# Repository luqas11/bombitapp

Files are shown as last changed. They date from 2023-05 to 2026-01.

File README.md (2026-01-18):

# bombitapp

### What is this
This project is a **device that controls and protects electric water pump systems**, built with an **ESP8266** based board, and operated from a mobile app developed in [React Native](https://reactnative.dev/). The device is able to preventively cut off power from the pump engines when an abnormal functioning is detected.

It's designed to operate over this preexisting pump setup:
- 2 220VAC 1/2 HP pumps.
- 2 water tanks.
- 2 water level sensors, placed inside the tanks and made by an on/off switch that turns on when the tank gets emptied and turns off when the filling process is complete. That switch operates directly at 220VAC and it's signal is plugged in to the pumps.
- 2 separated pipe circuits, each one connected to a different tank and pump. 

For different mechanical reasons, the sensors sometimes fail and keep the pumps engines running indefinitely, until manually fixed. If this happens, both the engines and the tanks could result **physically damaged** if the problem isn't solved quickly. This device's idea is to **cut pump power** if the sensor is sending the signal over a time period that exceeds some predefined threshold, to protect the setup. From a mobile app, the user can **resume the power after fixing the problem**, or **read the tank filling time history** to get an idea of the expected values. 

### Components
The project has the following components and features:

##### Hardware
- An ESP8266 based board, able to connect to the home Wi-Fi network.
- A custom PCB, to allow the ESP mounting and connection to the inputs and ouputs.
- 2 220VAC inputs, to recieve the tank water level signal. The ESP will read that signal to make it's decissions.
- 2 220VAC outputs, to power the water pumps. The ESP will power them with the water level sensor signal or not, depending on it's decissions.
- 1 5VCC input, to power the ESP board.
- 1 LED to indicate the WiFi connection status.

##### Firmware
- A sketch written in C++ and loaded to the ESP.
- Serves a webpage that allows the user to initially configure the WiFi credentials.
- Allows the level sensor signal to reach the output and power the pump until a time threshold is exceeded. After that, the connection is stopped to prevent the engine to keep working. If the signal stops before the threshold (i. e. the filling was successful), nothing happens.
- The time threshold can be setted via an HTTP request.
- Allows to resume the pump power via an HTTP request, overriding the stop state.
- The current engine working time can be get with an HTTP request.
- Allows to see the latest 10 engine run times via an HTTP request.
- Allows to see an average of all the previous engine run times via an HTTP request.
- The water level sensor status can be seen via an HTTP request (i. e. if it's on or off).

##### Mobile App
- A React Native mobile app compiled for Android.
- Gives a nice and human-friendly presentation layer for the firmware interaction, showing engine status and actions that can be made through HTTP.

### Screenshots
##### Mobile App
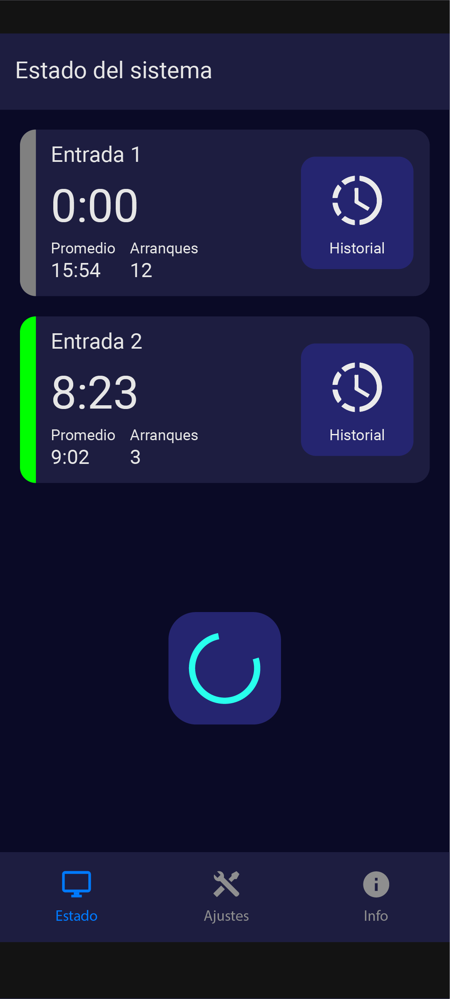
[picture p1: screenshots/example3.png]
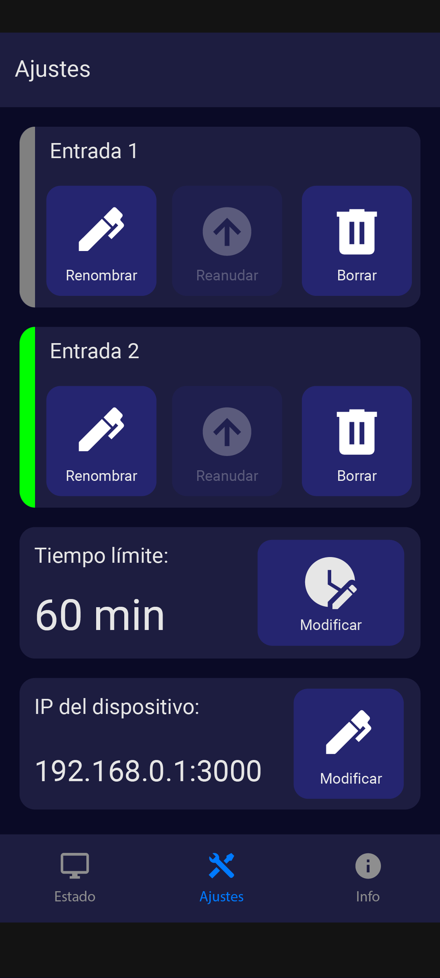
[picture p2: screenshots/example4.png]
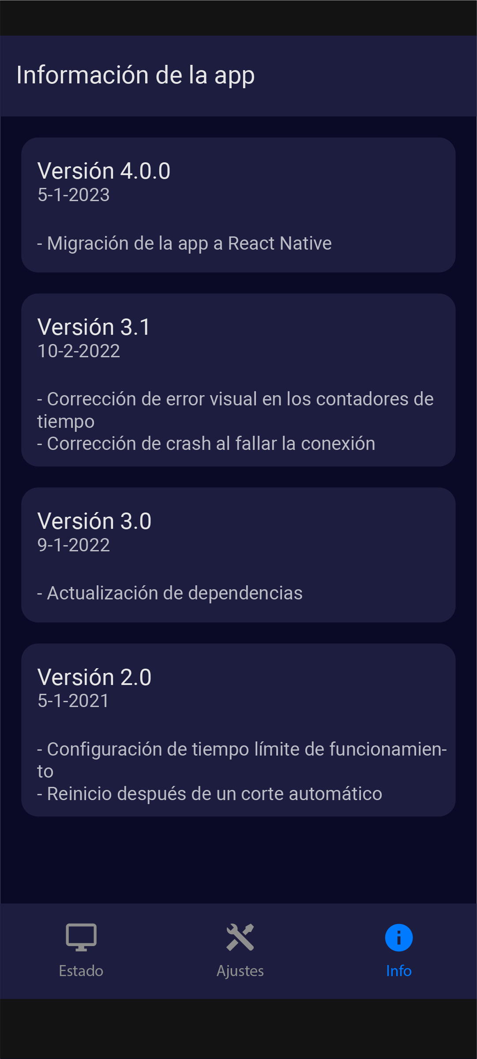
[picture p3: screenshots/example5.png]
    

##### PCB 3D model
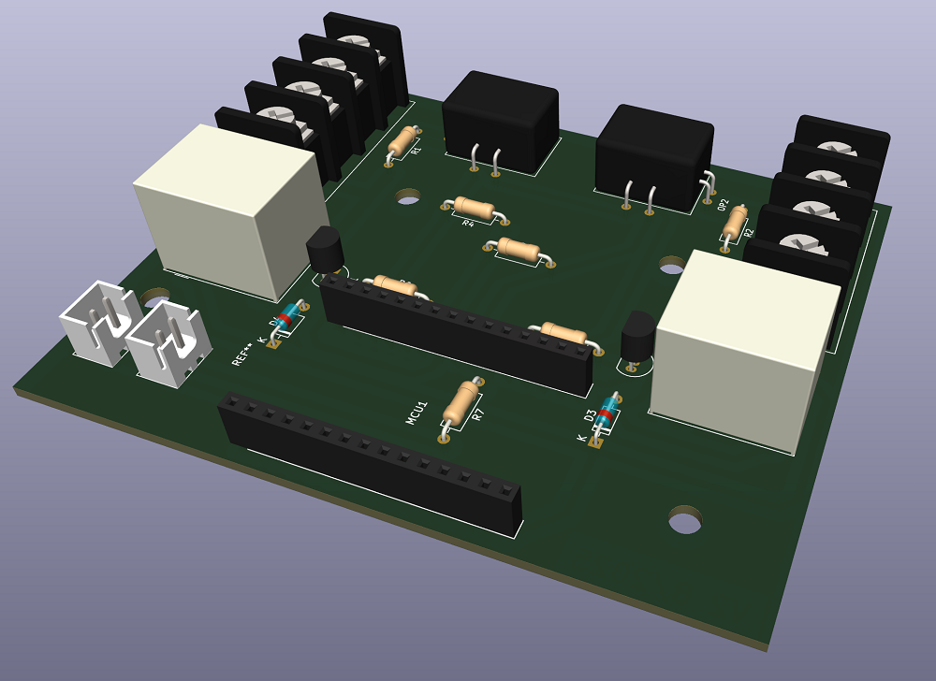
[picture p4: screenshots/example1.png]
 

##### Circuit schematic
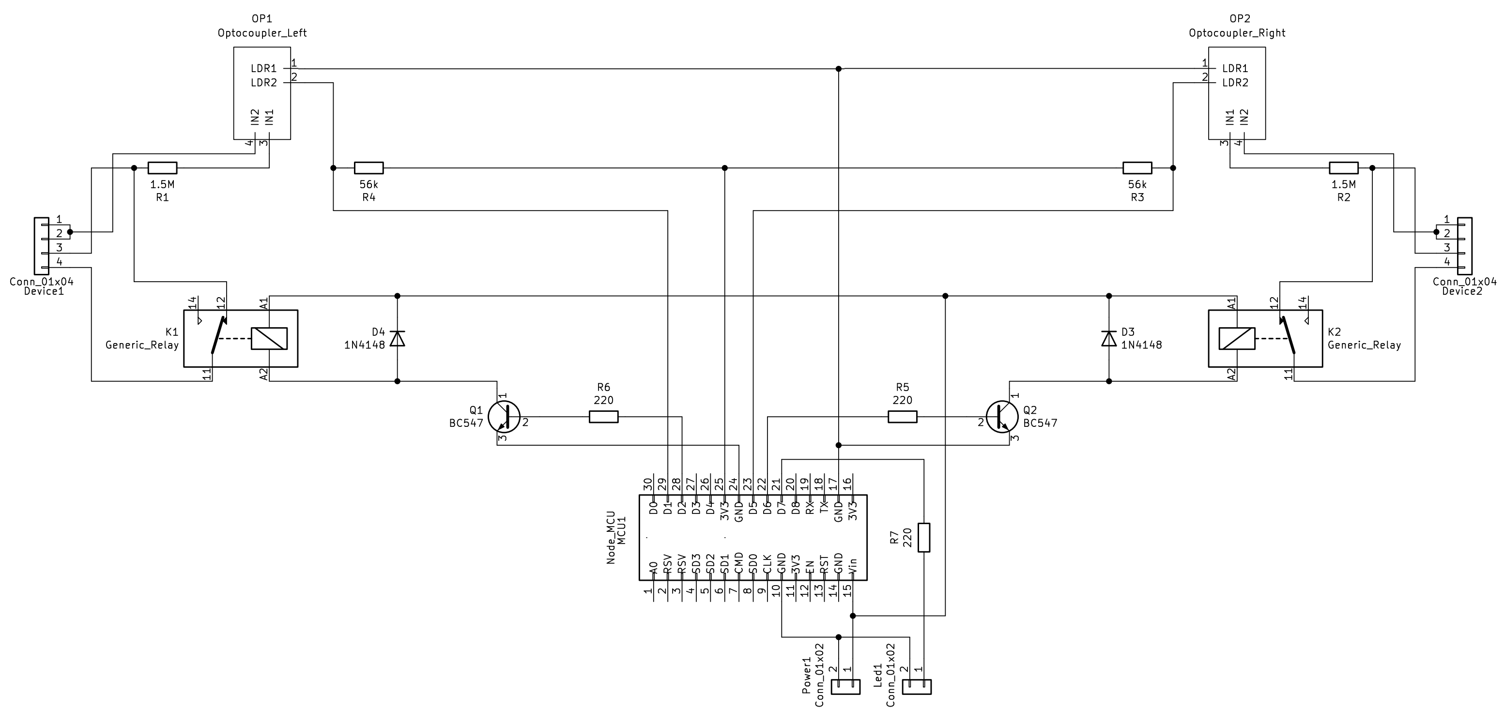
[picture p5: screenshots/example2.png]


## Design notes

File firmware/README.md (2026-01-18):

# Firmware

### How this works
This ESP8266 sketch connects the board to the WiFi network, and exposes some endpoints to get system status and set system configuration. The [Postman](https://www.postman.com/) collection in the root directory of this repository has complete examples and use cases of this API.

### API

`[GET] /status`  

Returns the current system status, including input status, device status, run counts and more. For example:
```
{
    "time_limit": 60,
    "devices": [
        {
            "status": 0,
            "current_time": 0,
            "mean_time": 25,
            "run_count": 10,
            "input_status": false,
            "history": [
                34,
                9,
                9,
                25,
                30,
                16,
                19,
                29,
                54,
                57
            ]
        },
        {
            "status": 0,
            "current_time": 0,
            "mean_time": 50,
            "run_count": 3,
            "input_status": false,
            "history": [
                28,
                42,
                81,
                0,
                0,
                0,
                0,
                0,
                0,
                0
            ]
        }
    ]
}
```

`[GET] /clear-history?device={id}`  

Clears the run time history of a specific device. For example, the query params could be:
```
/clear-history?device=0
```

`[GET] /change-time-limit?time_limit={time}`  

Sets the run time limit in minutes to trigger the forced stop mode, for all the devices in the system. For example, the query params could be:
```
/change-time-limit?time_limit=60
```

`[GET] /resume?device={id}`  

Resumes a device that is in forced stop mode. For example, the query params could be:
```
/resume?device=0
```

`[GET] /get-wifi-config`  

Returns the current WiFi configuration. For example:
```
{
    "ssid": "myssid"
}
```

`[GET] /set-wifi-config?ssid={ssid}&password={password}`  

Sets the WiFi configuration with the specified SSID and password. For example, the query params could be:
```
/set-wifi-config?ssid=myssid&password=mypassword
```

`[GET] /get-wifi-status`  

Returns the current WiFi connection status and IP address. For example:
```
{
    "status": 3,
    "ip": "192.168.1.100"
}
```

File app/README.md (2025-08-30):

# App
This **React Native** app allows the end-user to see the system status, and set the system configurations.

With it, the user can:
- See the current devices statuses
- See the run time history
- See the average run time
- Set the time threshold to stop a device
- Clear run time history
- Set the system IP, to send the requests to

### Development notes:
There is a mock created with [JSON Server](https://github.com/typicode/json-server/tree/v0) that allows the developer to have working endpoints to test the app against, without having to run the firmware in a board. The mock IP can be configured in the `mock` script inside the `package.json` file.

To launch the app in a device or an emulator, use:  
`npm run android`

To compile an APK, use:  
`npm run assemble`

To start the mock server, use:  
`npm run mock`

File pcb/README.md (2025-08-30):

# PCB

This is a PCB design that implements the connections between the 220VAC relays and optocoupliers and the ESP board, along with all the necessary 3D printed parts to enable component mounting. The circuit schematic and the PCB layout are printed in the `pcb-schematic.pdf` and `pcb-layout.pdf` files respectively.

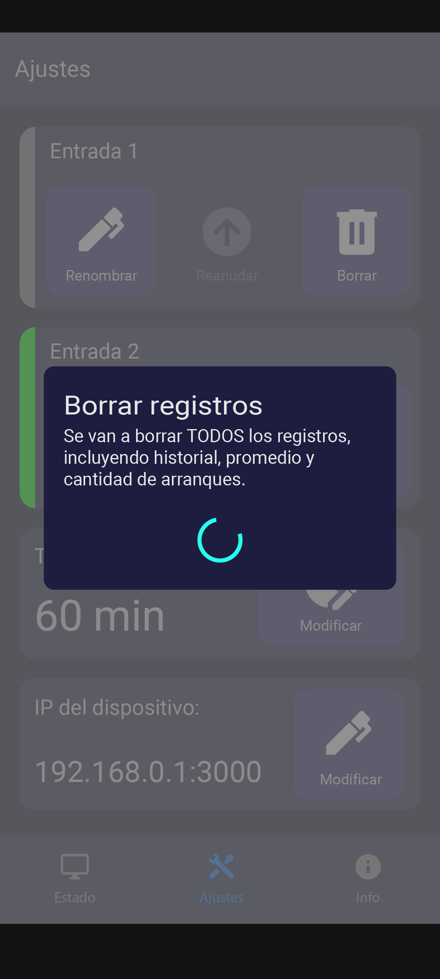
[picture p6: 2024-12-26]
app/ui_design/config_dialog_question_loading.png

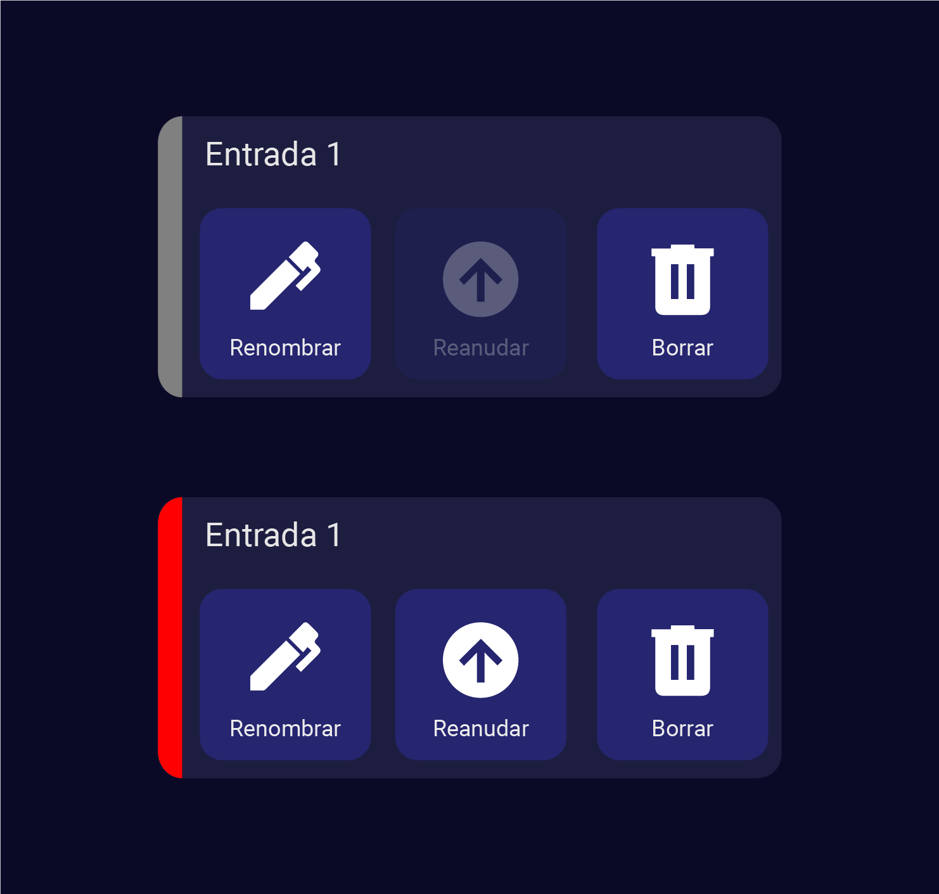
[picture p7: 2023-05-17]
app/ui_design/config_states.png

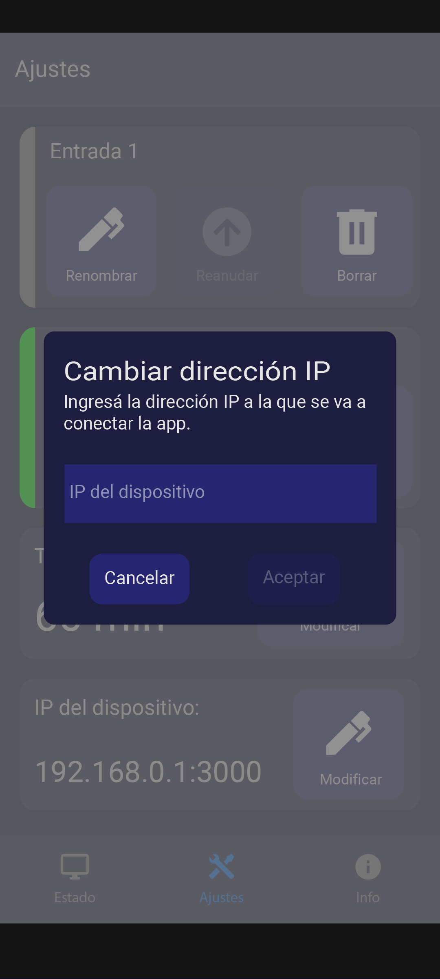
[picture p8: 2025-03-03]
app/ui_design/config_dialog_question_input_2.png

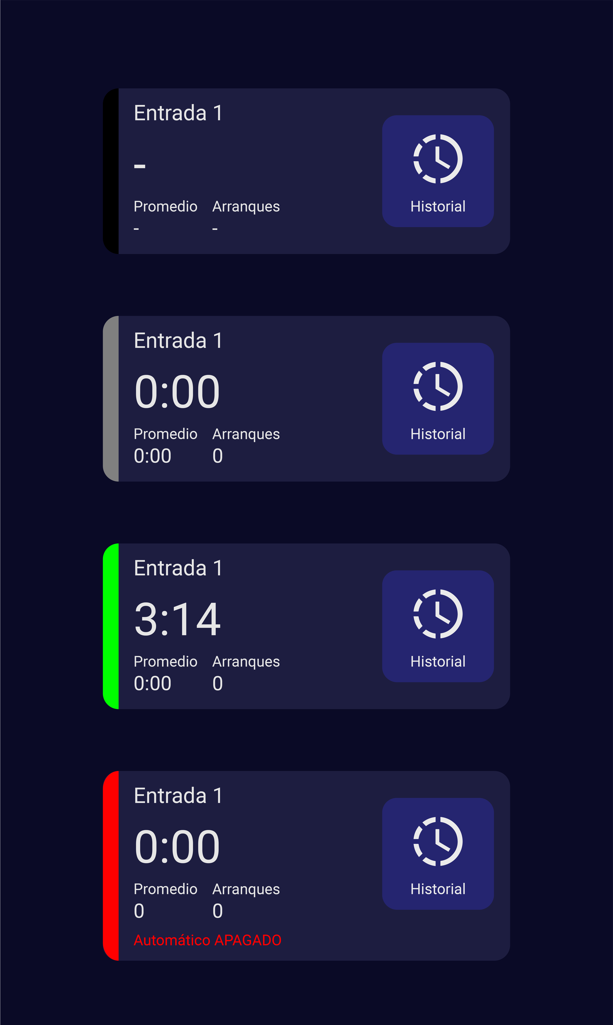
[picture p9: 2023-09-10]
app/ui_design/ouputs_statuses.png

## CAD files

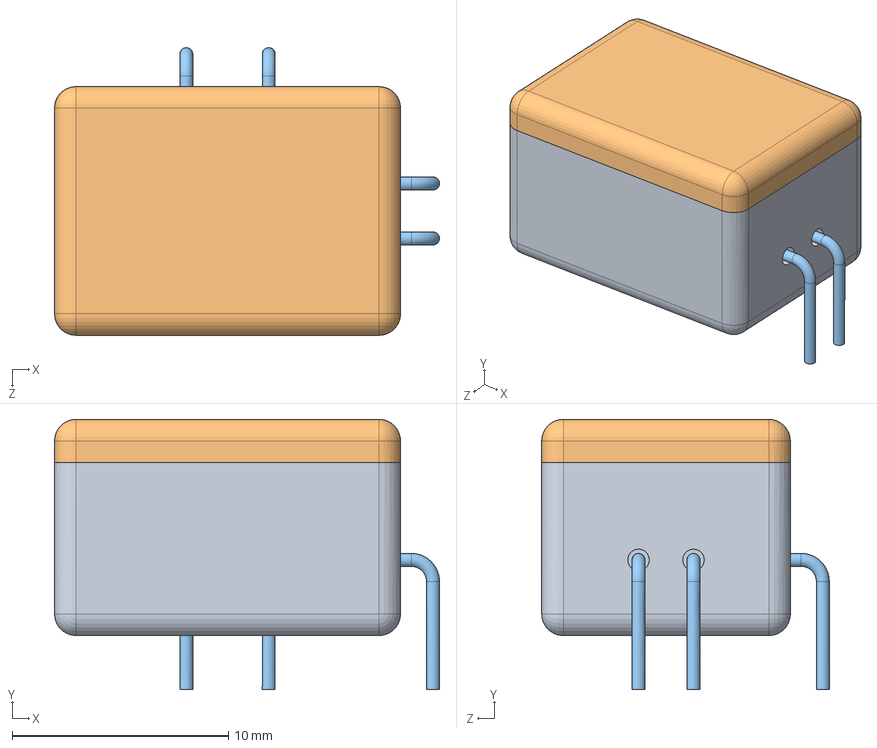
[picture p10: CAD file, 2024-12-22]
pcb/3D models/optocoupler.SLDASM
17.8 x 12.5 x 13.3 mm
optocoupler_box
optocoupler_lid
optocoupler_pin x 4

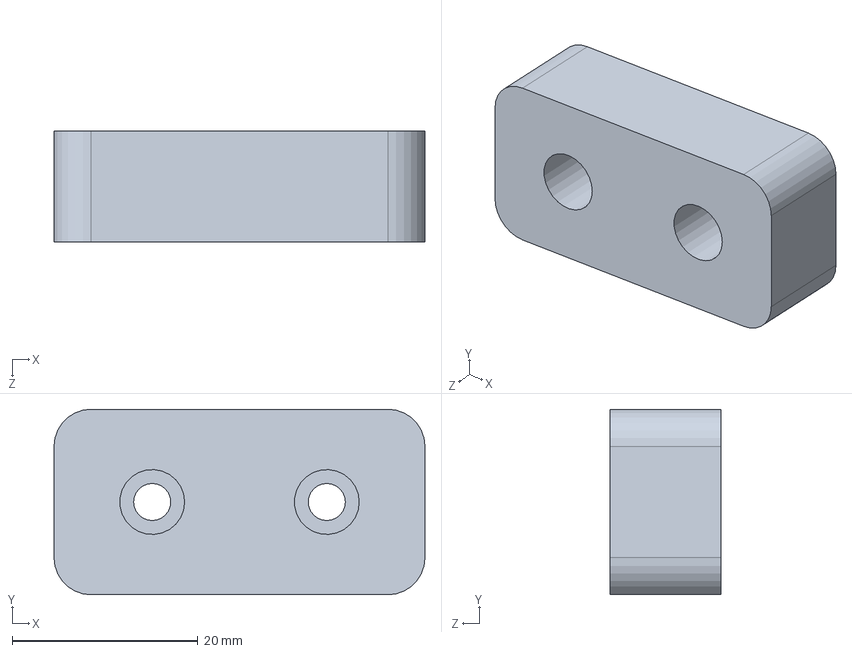
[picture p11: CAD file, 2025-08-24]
pcb/3D models/status_led_case.SLDPRT
40.0 x 20.0 x 12.0 mm

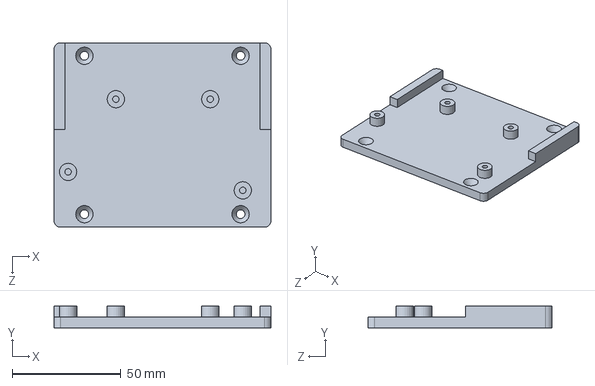
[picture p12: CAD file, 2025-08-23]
pcb/3D models/pcb_support.SLDPRT
100.0 x 10.0 x 85.0 mm

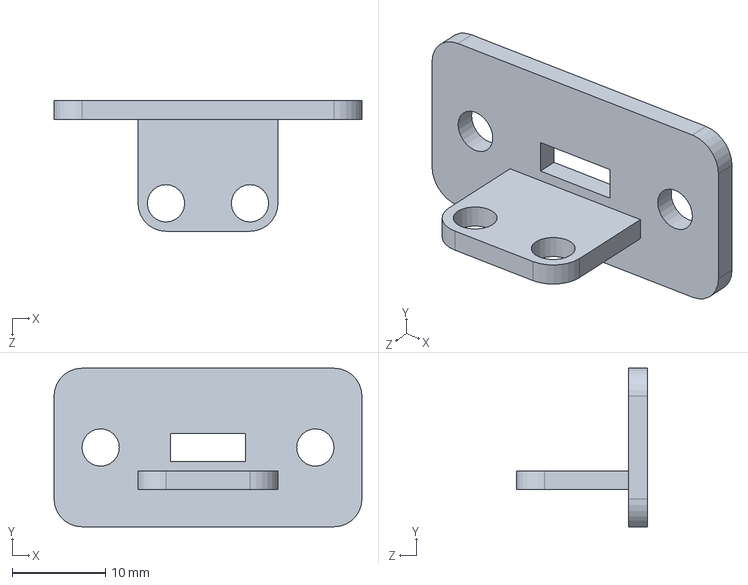
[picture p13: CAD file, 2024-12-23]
pcb/3D models/power_usb_socket.SLDPRT
33.0 x 17.0 x 14.0 mm

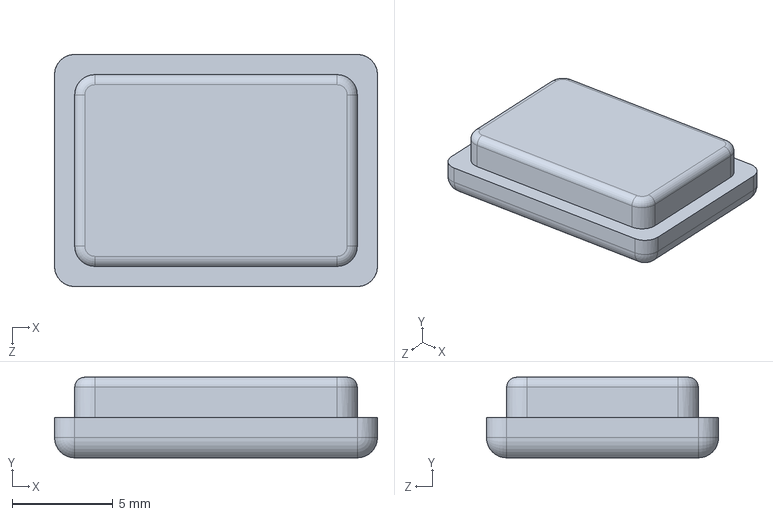
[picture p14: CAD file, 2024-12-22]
pcb/3D models/optocoupler_lid.SLDPRT
16.0 x 4.00 x 11.5 mm

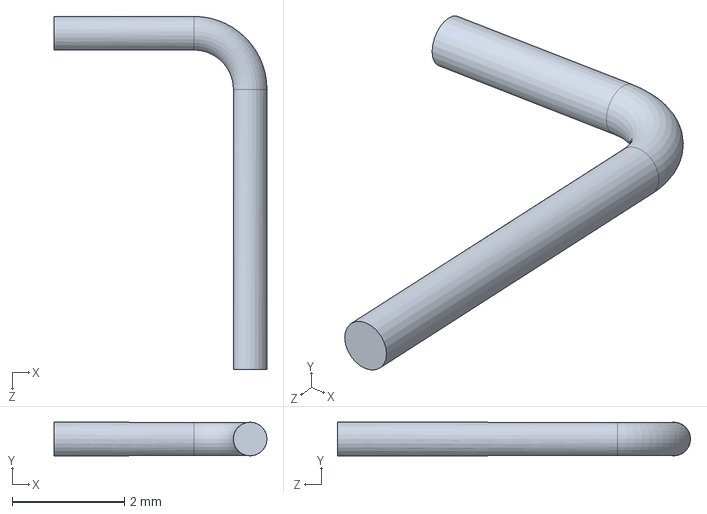
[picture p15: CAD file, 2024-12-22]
pcb/3D models/optocoupler_pin.SLDPRT
3.80 x 0.6 x 6.30 mm

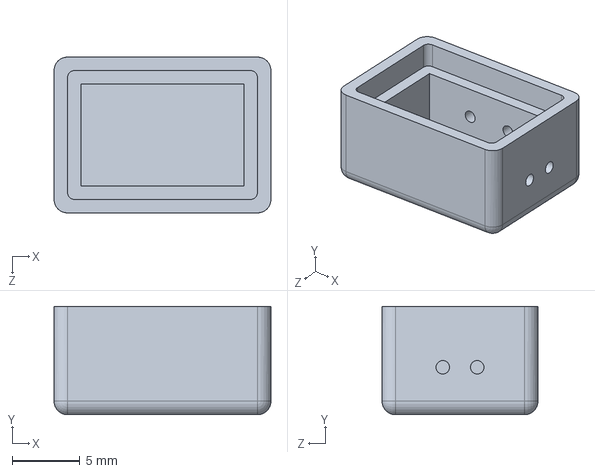
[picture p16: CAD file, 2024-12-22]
pcb/3D models/optocoupler_box.SLDPRT
16.0 x 8.00 x 11.5 mm

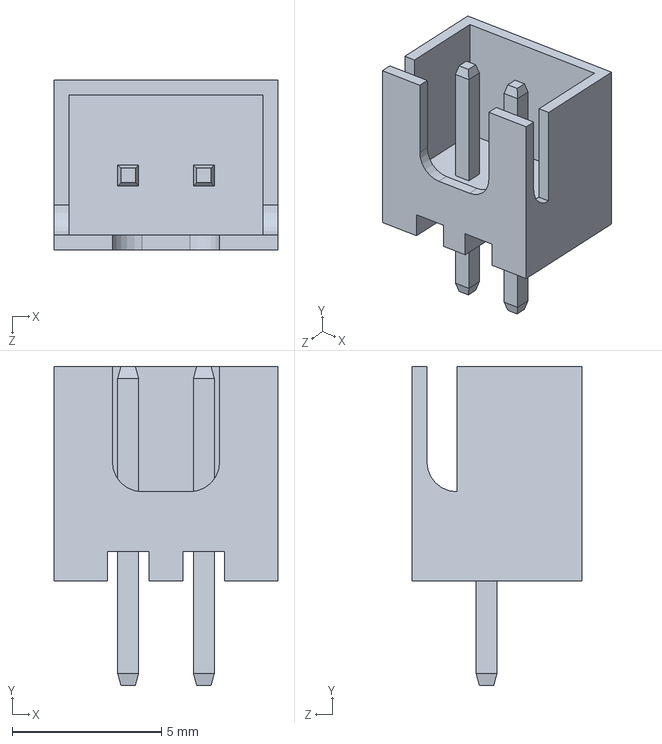
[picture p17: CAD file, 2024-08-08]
pcb/3D models/Pin_socket_2.SLDPRT
7.50 x 10.7 x 5.70 mm

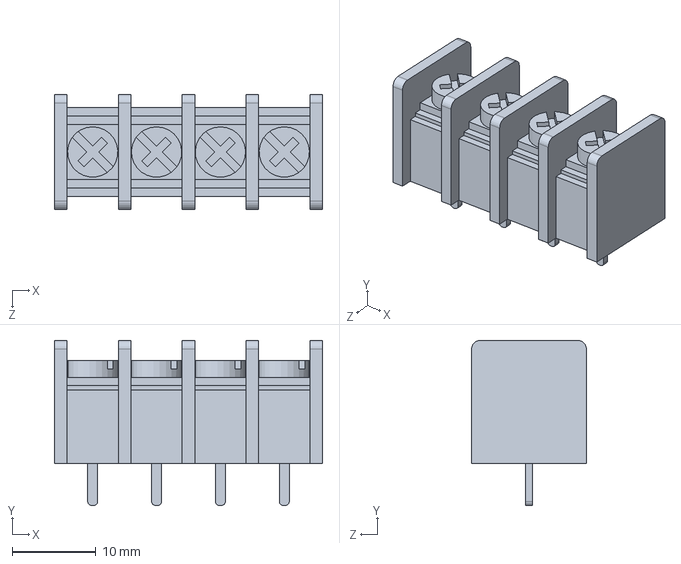
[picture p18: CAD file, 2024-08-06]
pcb/3D models/Terminal_block_4.SLDPRT
32.0 x 19.7 x 13.7 mm

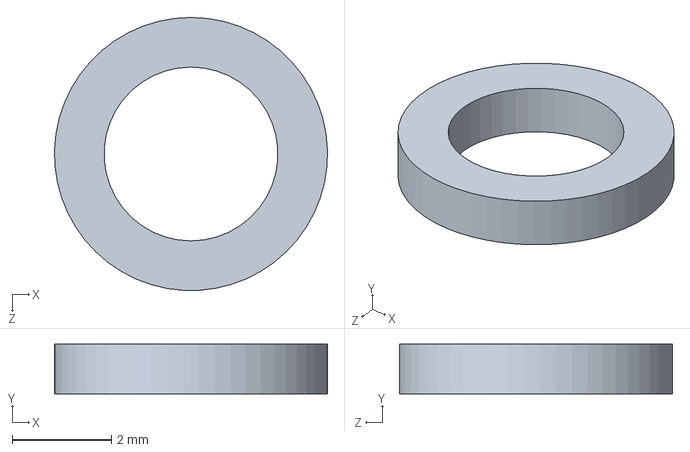
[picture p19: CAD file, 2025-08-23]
pcb/3D models/power_usb_washer.SLDPRT
5.50 x 1.00 x 5.50 mm

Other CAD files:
pcb/3D models/optocoupler_box.STL
pcb/3D models/optocoupler_lid.STL
pcb/3D models/pcb_support.STL
pcb/3D models/power_usb_socket.STL
pcb/3D models/power_usb_washer.STL
pcb/3D models/status_led_case.STL

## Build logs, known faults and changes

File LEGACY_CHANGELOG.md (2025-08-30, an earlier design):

# Control de bombas

## Versión 4.0.0 (5/1/2023)
*Prototipo probado con PCB, dos bombas y caja estanca.*
#### Android:
- Migración de la app a React Native

#### Software:
- Mejora de las respuestas de error
- Refactoreo de la lógica para recibir comandos

## Versión 3.1 (10/2/2022)

#### Android:
- Corrección de errores
- Actualización de dependencias

## Versión 3.0 (9/1/2022)
*Prototipo probado con PCB, dos bombas y caja estanca.*
#### Hardware:
- Rediseño del PCB para hacerlo más compacto y corregir errores
- Cambio de optoacopladores de 5V-5V por 220V-5V
- Construcción del nuevo PCB
- Armado de caja estanca con soporte para el PCB y tomas hembra para las bombas

## Versión 2.0 (4/1/2021)
*Prototipo probado con PCB propio y una única bomba.*
#### Software:
- Refactoreo de código general
- Parametrización de las direcciones de memoria de la EEPROM
- Refactoreo de variables para permitir escalabilidad a *n* entradas
- Respuestas de request formateadas como JSON
- Corte automático en caso de falla y reanudación manual
- Capacidad de recibir comandos para configurar el tiempo de corte automático, activar la reanudación manual y limpiar valores en EEPROM

#### Hardware:
- Diseño y construcción de PCB
- Dos entradas optoacopladas 5V-5V
- Dos salidas con relé 5V-220V

## Versión 1.x (N/A) 
*Prototipo probado en versión cableada, sin PCB y con dos bombas.*
#### Software:
- Guardado de tiempos en memoria EEPROM
- Comunicación vía HTTP request
- Respuesta en texto plano sin parsear, con estado actual de las bombas, historiales y promedios
- Entradas para dos bombas 

#### Hardware:
- Construcción de circuito cableado
- Dos entradas directas a 5V

## Versión 0.x (N/A)  
Sin documentar.

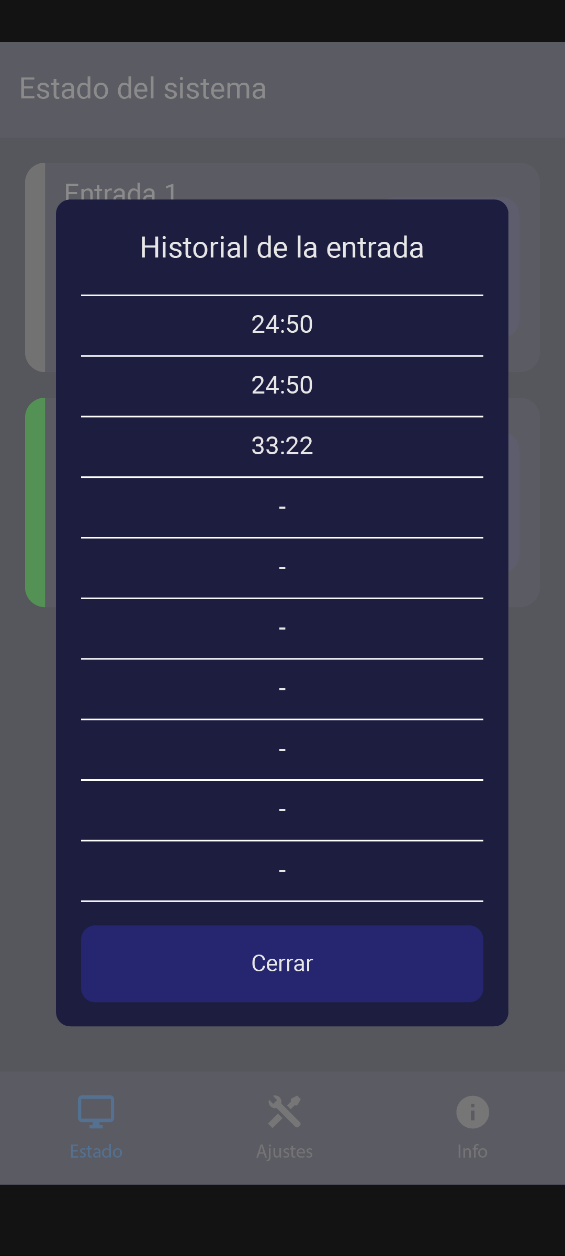
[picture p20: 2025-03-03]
app/ui_design/status_history.png

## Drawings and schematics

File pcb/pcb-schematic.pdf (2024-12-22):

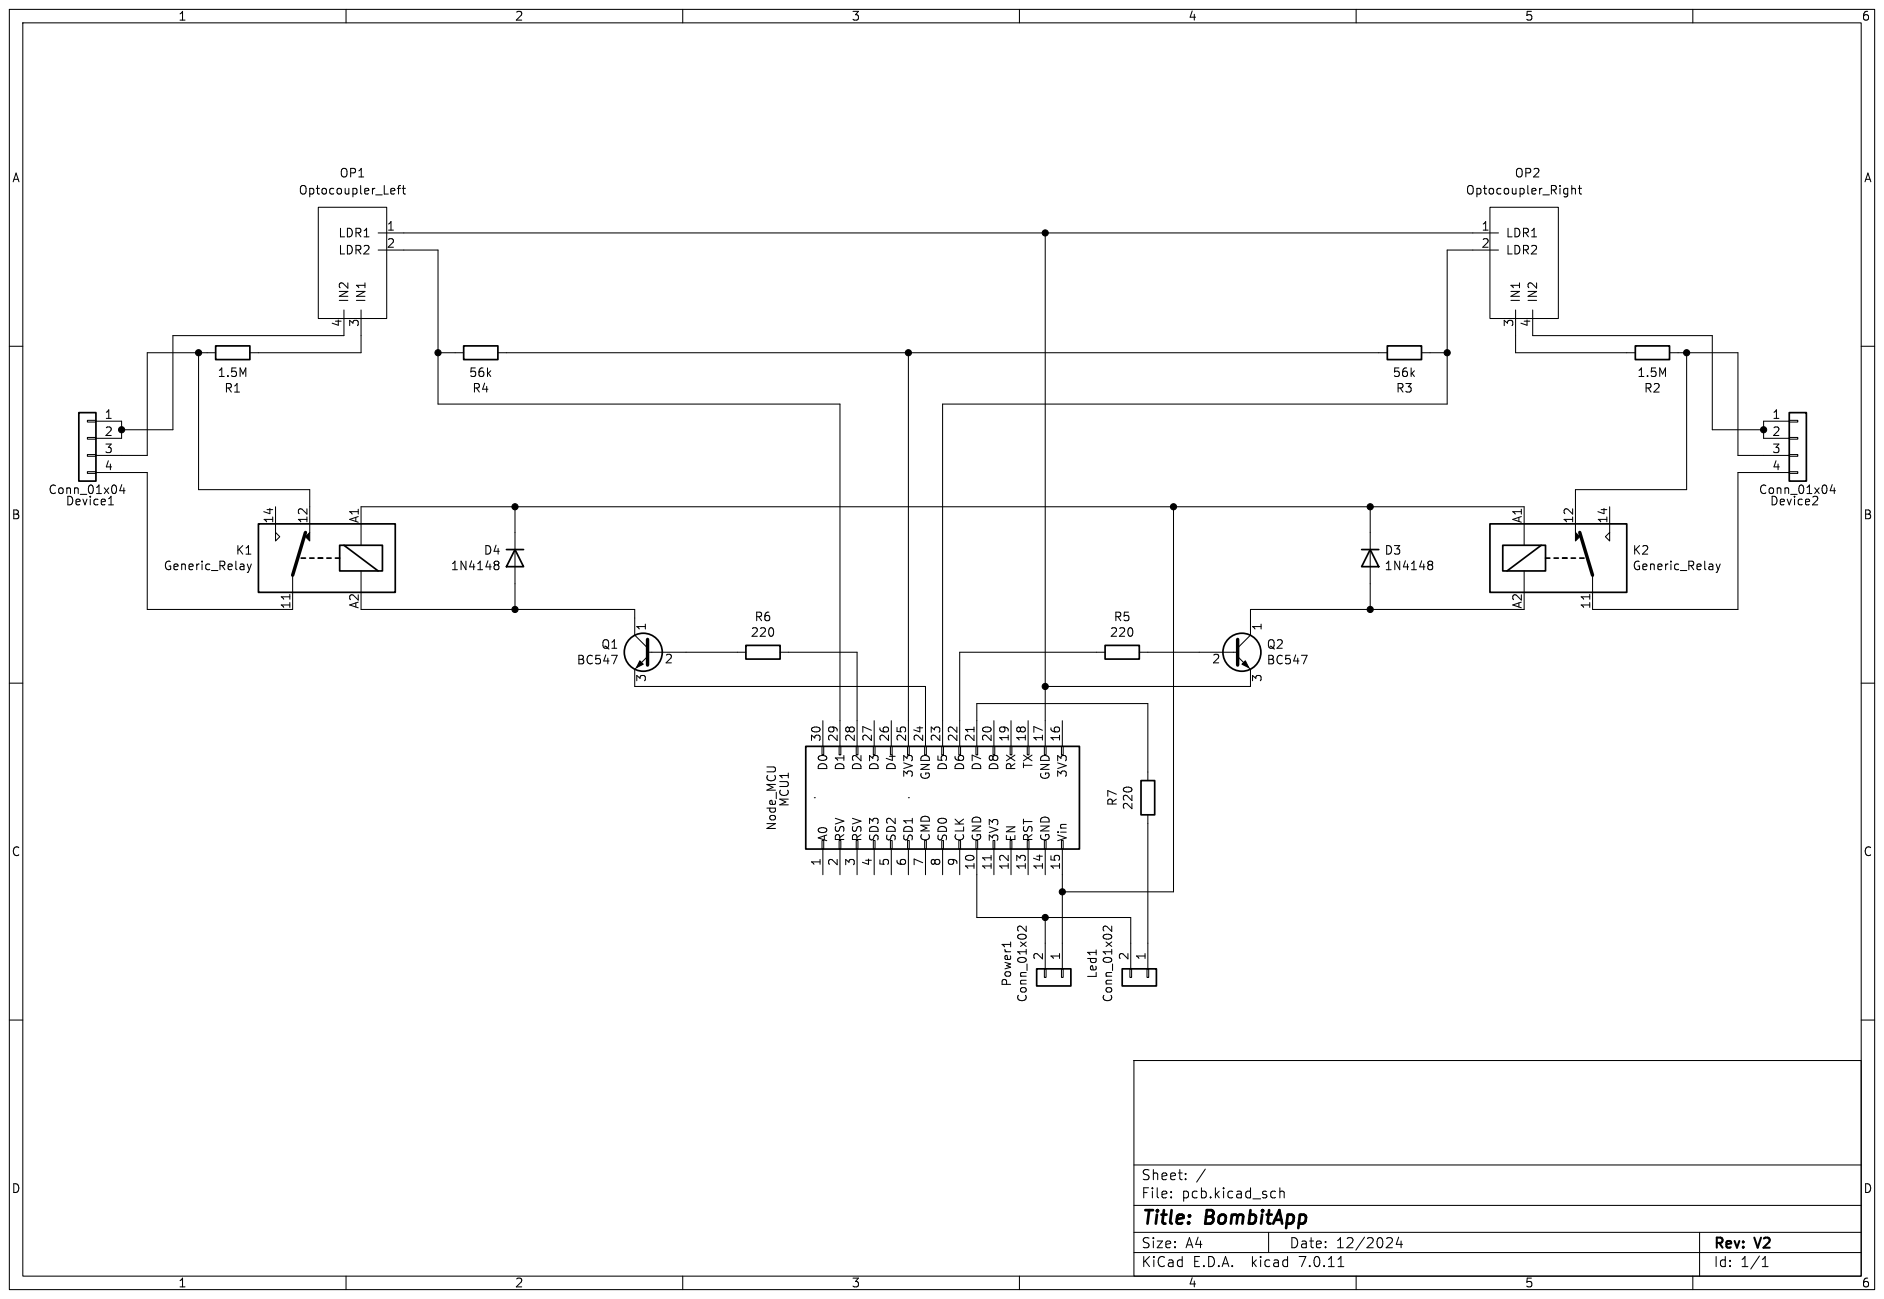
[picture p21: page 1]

1 GND 10 3V3 11 EN 12 RST 13 GND 14 Vin 15 3V3 16 GND 17 TX 18 RX 19 RSV

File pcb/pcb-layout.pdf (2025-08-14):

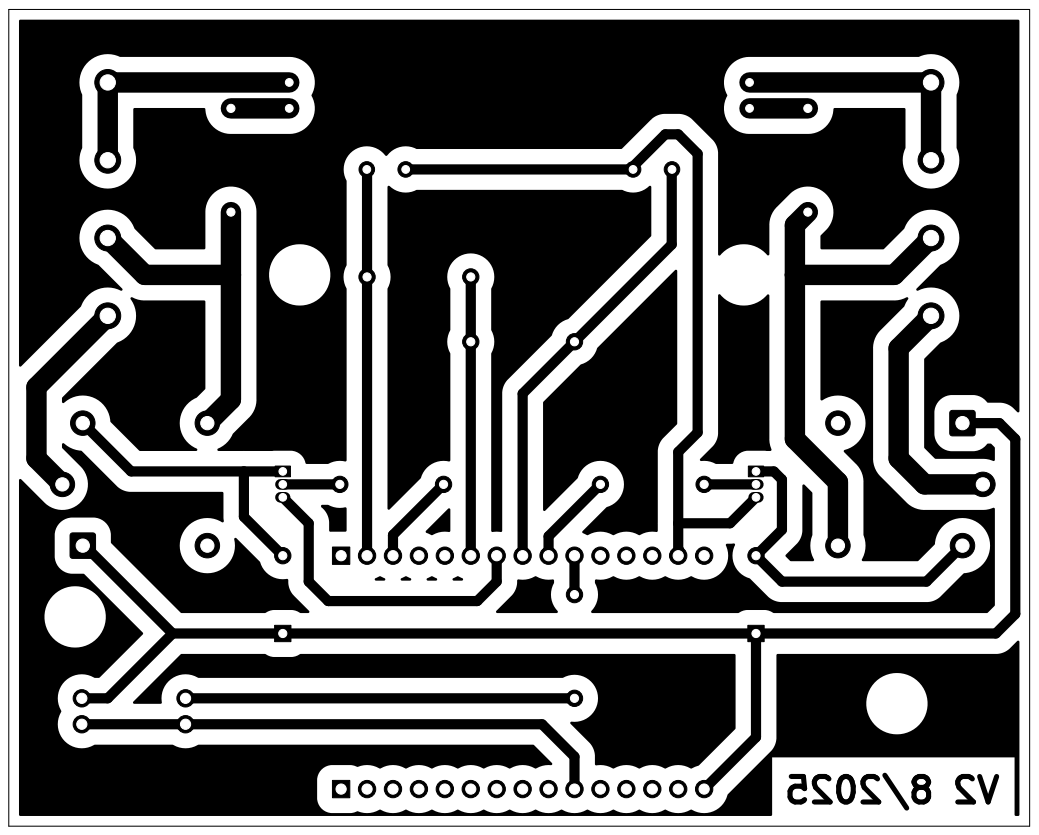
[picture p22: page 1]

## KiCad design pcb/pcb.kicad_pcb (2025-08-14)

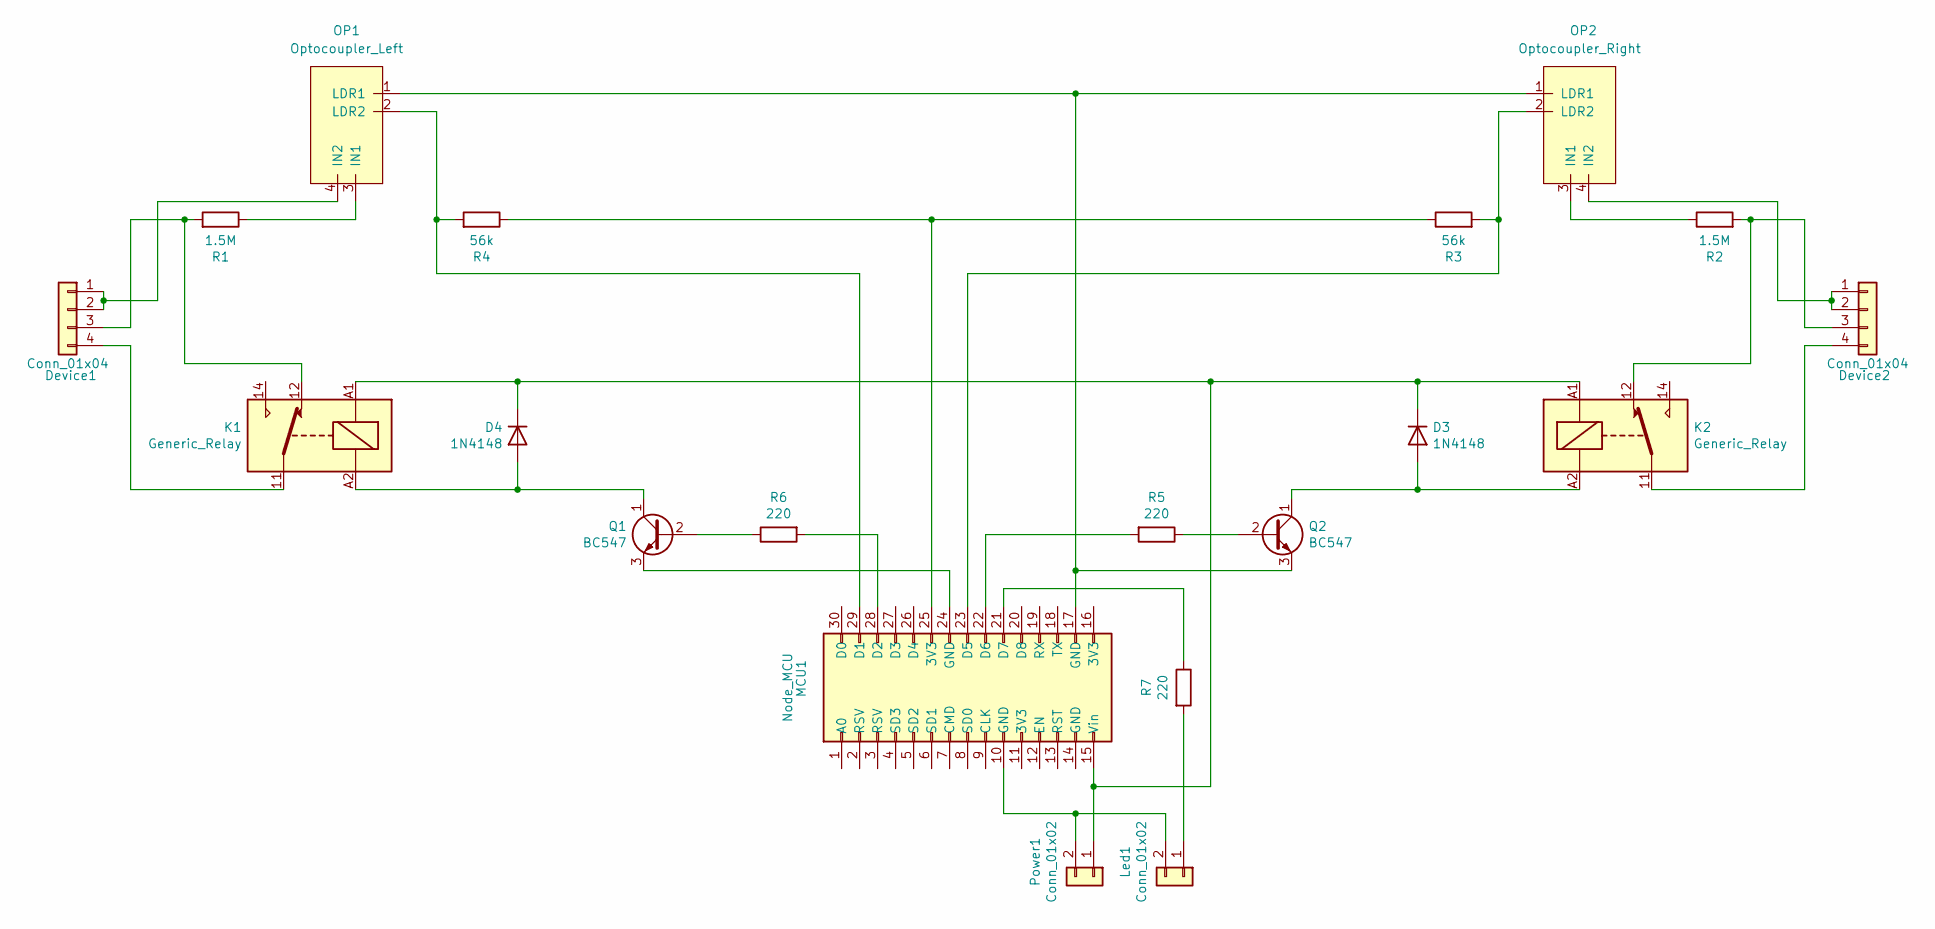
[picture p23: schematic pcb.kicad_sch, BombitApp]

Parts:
D3, D4: 1N4148; D_DO-35_SOD27_P7.62mm_Horizontal
Device1, Device2: Conn_01x04; TerminalBlock_1x04
K1, K2: Generic_Relay; Relay_SPDT_Finder_36.11
Led1: Conn_01x02; PinSocket_1x02
MCU1: Node_MCU
OP1: Optocoupler_Left
OP2: Optocoupler_Right
Power1: Conn_01x02; PinSocket_1x02
Q1, Q2: BC547; TO-92_Inline
R1, R2: 1.5M; R_Axial_DIN0207_L6.3mm_D2.5mm_P10.16mm_Horizontal
R3, R4: 56k; R_Axial_DIN0207_L6.3mm_D2.5mm_P10.16mm_Horizontal
R5, R6, R7: 220; R_Axial_DIN0207_L6.3mm_D2.5mm_P10.16mm_Horizontal

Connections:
unnamed: D3.2 (A), K2.A2, Q2.1 (C)
unnamed: D3.1 (K), D4.1 (K), K1.A1, K2.A1, MCU1.15 (Vin), Power1.1
unnamed: D4.2 (A), K1.A2, Q1.1 (C)
unnamed: Device1.1, Device1.2, OP1.4 (IN2)
unnamed: Device1.3, K1.12, R1.2
unnamed: Device1.4, K1.11
unnamed: Device2.1, Device2.2, OP2.4 (IN2)
unnamed: Device2.3, K2.12, R2.2
unnamed: Device2.4, K2.11
unnamed: Led1.1, R7.2
unnamed: Led1.2, MCU1.10 (GND), Power1.2
unnamed: MCU1.25 (3V3), R3.1, R4.1
unnamed: MCU1.29 (D1), OP1.2 (LDR2), R4.2
unnamed: MCU1.28 (D2), R6.2
unnamed: MCU1.23 (D5), OP2.2 (LDR2), R3.2
unnamed: MCU1.22 (D6), R5.2
unnamed: MCU1.21 (D7), R7.1
unnamed: OP1.3 (IN1), R1.1
unnamed: MCU1.17 (GND), OP1.1 (LDR1), OP2.1 (LDR1), Q2.3 (E)
unnamed: OP2.3 (IN1), R2.1
unnamed: Q1.2 (B), R6.1
unnamed: MCU1.24 (GND), Q1.3 (E)
unnamed: Q2.2 (B), R5.1

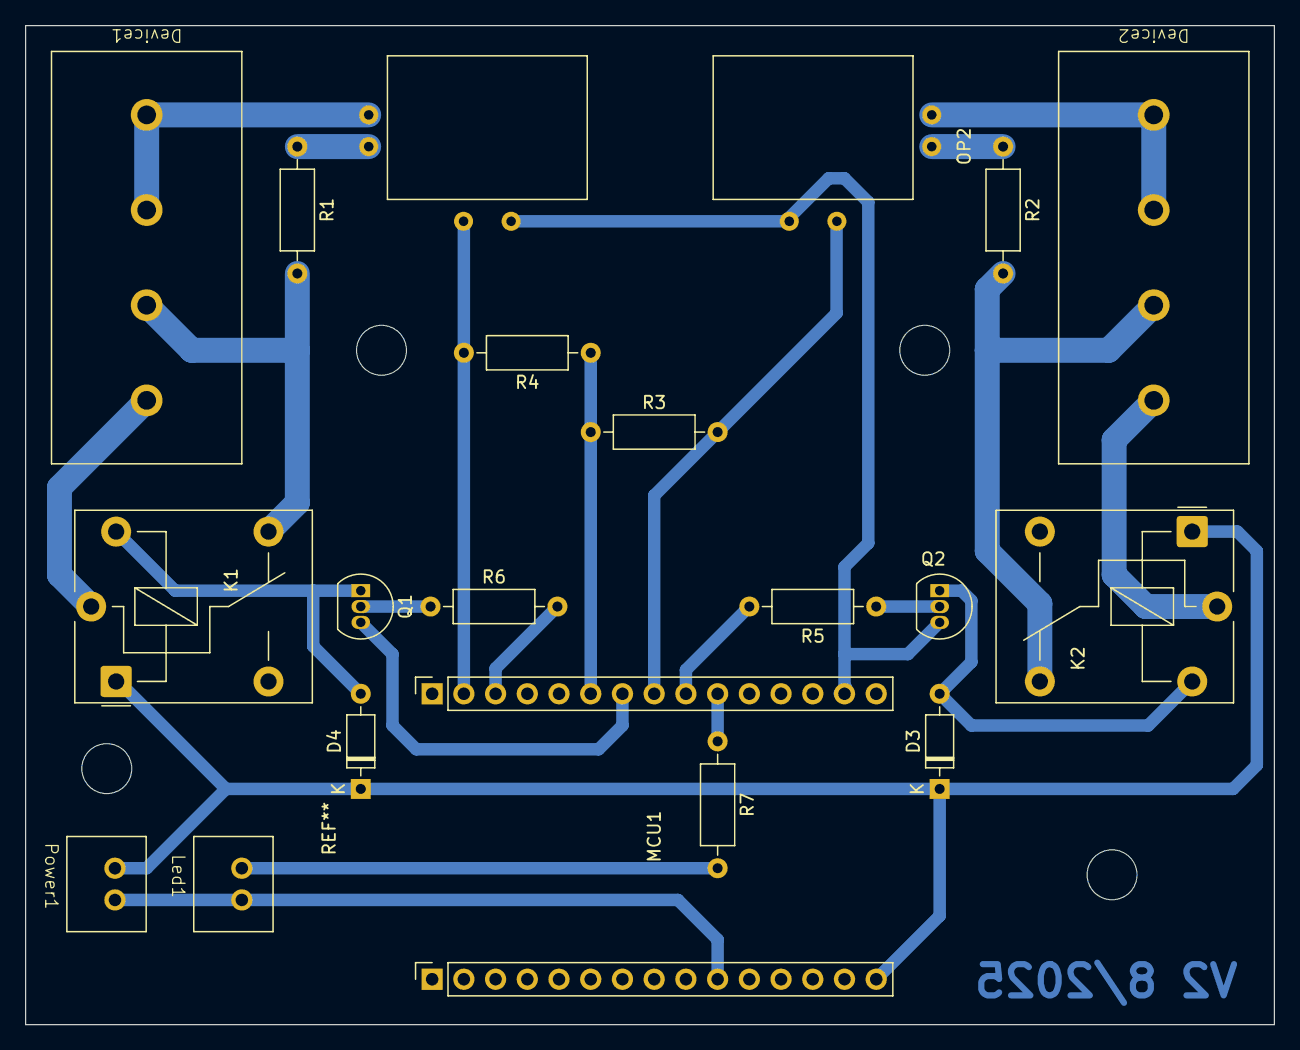
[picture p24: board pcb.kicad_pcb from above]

Board: 2 copper layers, 100.0 x 80.0 mm, 20 parts (0 on the bottom side), 23 nets.

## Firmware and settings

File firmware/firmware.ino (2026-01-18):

#include <ESP8266WebServer.h>
#include <ESP8266WiFi.h>
#include "JSONUtils.h"
#include "WiFiUtils.h"
#include "EEPROMUtils.h"
#include "DataTypes.h"
#include "config.h"
#include "AdminPage.h"

/*
   Version 5.1.0
   18-1-2026

   External libraries:
   ArduinoJson@7.4.2
   esp8266@3.1.2
*/

// LED pin to indicate the network connection status
const int STATUS_LED = 13;
// Duration of the status LED blinks
const int LED_BLINK_TIME = 100;
// Number of devices connected to the system
const int DEVICES_NUMBER = 2;
// Default running time limit in minutes
const uint16_t DEFAULT_TIME_LIMIT = 30;
// Inputs pin numbers
const int INPUTS_PINS[DEVICES_NUMBER] = { 5, 14 };
// Outputs pin numbers
const int OUTPUTS_PINS[DEVICES_NUMBER] = { 4, 12 };
// Input debounce time in seconds
const int DEBOUNCE_TIME = 3;

// Status constants
const int OFF = 0;
const int RUNNING = 1;
const int STOPPED = 2;

// Error codes
const String NOT_FOUND = "ERR_00";
const String INVALID_TIME_LIMIT = "ERR_01";
const String INVALID_DEVICE = "ERR_02";
const String DEVICE_NOT_STOPPED = "ERR_03";
const String INVALID_WIFI_SSID = "ERR_04";
const String INVALID_WIFI_PASSWORD = "ERR_05";

// Memory addresses
const int LIMIT_ADDR = 0;
const int MEAN_ADDR = LIMIT_ADDR + 1;
const int COUNT_ADDR = MEAN_ADDR + DEVICES_NUMBER;
const int HISTORY_ADDR = COUNT_ADDR + DEVICES_NUMBER;

// State variables
DeviceData devicesData[DEVICES_NUMBER] = {};
uint16_t timeLimit = DEFAULT_TIME_LIMIT;
unsigned long lastLedTimestamp;
bool isLedBlinking;

// HTTP server instance
ESP8266WebServer server(80);

void setup() {
  // Initialize input and output pins
  pinMode(STATUS_LED, OUTPUT);
  for (int pin : INPUTS_PINS) {
    pinMode(pin, INPUT);
  }
  for (int pin : OUTPUTS_PINS) {
    pinMode(pin, OUTPUT);
    digitalWrite(pin, LOW);
  }

  // Initialize the serial communication, the EEPROM library, the WiFi connection and the devices state variables
  Serial.begin(115200);
  beginEEPROM();
  beginWiFi(SSID_AP, PASSWORD_AP, STATUS_LED);
  getSavedStateValues();

  // Set up all the server endpoints
  server.on("/admin", handleAdmin);
  server.on("/status", handleStatus);
  server.on("/clear-history", handleClear);
  server.on("/change-time-limit", handleChangeLimit);
  server.on("/resume", handleResume);
  server.on("/get-wifi-config", handleGetWiFiConfig);
  server.on("/set-wifi-config", handleSetWiFiConfig);
  server.on("/get-wifi-status", handleGetWiFiStatus);
  server.onNotFound(handleNotFound);

  // Initialize the HTTP server
  server.begin();
}

void loop() {
  // Handle any incoming request, if exists
  server.handleClient();

  // Set the LED state depending on the network status
  if (isLedBlinking != true) {
    digitalWrite(STATUS_LED, isWiFiConnected() ? LOW : HIGH);
  }

  // Turn on the status LED if the blink is finished
  if ((millis() - lastLedTimestamp) > LED_BLINK_TIME && isLedBlinking == true) {
    digitalWrite(STATUS_LED, LOW);
    isLedBlinking = false;
  }

  // Loop over the given number of devices, processing it's state
  for (int i = 0; i < DEVICES_NUMBER; i++) {
    // Whenever the device is running, update the current timer and make a forced stop if time limit is exceeded
    if (devicesData[i].status == RUNNING) {
      devicesData[i].currentTime = (millis() - devicesData[i].currentRunTimestamp) / 1000;
      if (devicesData[i].currentTime > timeLimit * 60) {
        devicesData[i].status = STOPPED;
        digitalWrite(OUTPUTS_PINS[i], HIGH);
      }
    }

    // Read the input state and save the debounce timestamp
    bool reading = !digitalRead(INPUTS_PINS[i]);
    if (reading != devicesData[i].lastChange) {
      devicesData[i].lastChangeTimestamp = millis();
      devicesData[i].lastChange = reading;
    }

    // Take the reading as valid after the debounce is completed
    if (((millis() - devicesData[i].lastChangeTimestamp) / 1000) > DEBOUNCE_TIME) {
      devicesData[i].inputStatus = reading;
    }

    // If the input is on, but the device is still off, turn on the device and save the timestamp
    if (devicesData[i].inputStatus == true && devicesData[i].status == OFF) {
      devicesData[i].status = RUNNING;
      devicesData[i].currentRunTimestamp = millis();
    }

    // If the input is off, but the device is still on, turn off the device and process the run values
    if (devicesData[i].inputStatus == false && devicesData[i].status == RUNNING) {
      devicesData[i].status = OFF;
      devicesData[i].meanTime = (devicesData[i].meanTime * devicesData[i].runCount + devicesData[i].currentTime) / (devicesData[i].runCount + 1);
      devicesData[i].runCount++;
      addValueToHistory(devicesData[i].currentTime, i);
      devicesData[i].currentTime = 0;

      writeToEEPROM(MEAN_ADDR + i, devicesData[i].meanTime);
      writeToEEPROM(COUNT_ADDR + i, devicesData[i].runCount);
      writeArrayToEEPROM(HISTORY_ADDR + i * HISTORY_LENGTH, devicesData[i].history, sizeof(devicesData[i].history));
    }
  }
}

// Read the values stored in the EEPROM and save them to the state variables
void getSavedStateValues() {
  uint16_t _timeLimit = readFromEEPROM(LIMIT_ADDR);
  if (_timeLimit != 0) {
    timeLimit = _timeLimit;
  }
  for (int i = 0; i < DEVICES_NUMBER; i++) {
    devicesData[i].meanTime = readFromEEPROM(MEAN_ADDR + i);
    devicesData[i].runCount = readFromEEPROM(COUNT_ADDR + i);
    uint16_t savedHistory[HISTORY_LENGTH];
    readArrayFromEEPROM(HISTORY_ADDR + i * HISTORY_LENGTH, savedHistory, sizeof(savedHistory));
    for (int j = 0; j < HISTORY_LENGTH; ++j) {
      devicesData[i].history[j] = savedHistory[j];
    }
  }
}

// Adds a value to the history array of a given device, removing the oldest one to keep a constant array size
void addValueToHistory(uint16_t value, int deviceNumber) {
  uint16_t newHistory[HISTORY_LENGTH];
  newHistory[0] = value;

  for (int i = 0; i < HISTORY_LENGTH - 1; i++) {
    newHistory[i + 1] = devicesData[deviceNumber].history[i];
  }
  for (int i = 0; i < HISTORY_LENGTH; ++i) {
    devicesData[deviceNumber].history[i] = newHistory[i];
  }
}

// Returns the current devices status to the client, formatted as a JSON string
void handleStatus() {
  String response = formatStatus(timeLimit, devicesData, DEVICES_NUMBER);
  server.send(200, "application/json", response);
  blinkStatusLed();
}

// Clears the recorded history, mean time and run count for the specified device, validating the user input
void handleClear() {
  String device = server.arg("device");
  char *end;
  long i = strtol(device.c_str(), &end, 10);
  if (device == "" || *end != '\0' || i > DEVICES_NUMBER - 1 || i < 0) {
    String response = formatError(INVALID_DEVICE, "Invalid device number");
    server.send(404, "application/json", response);
  } else {
    devicesData[i].meanTime = 0;
    devicesData[i].runCount = 0;
    for (int j = 0; j < HISTORY_LENGTH; j++) {
      devicesData[i].history[j] = 0;
    }
    writeToEEPROM(MEAN_ADDR + i, 0);
    writeToEEPROM(COUNT_ADDR + i, 0);
    writeArrayToEEPROM(HISTORY_ADDR + i * HISTORY_LENGTH, devicesData[i].history, sizeof(devicesData[i].history));
    server.send(200);
  }
  blinkStatusLed();
}

// Changes the running time limit for all the devices, validating the user input
void handleChangeLimit() {
  String time_limit = server.arg("time_limit");
  char *end;
  long newTimeLimit = strtol(time_limit.c_str(), &end, 10);
  if (time_limit == "" || *end != '\0' || newTimeLimit > UINT16_MAX || newTimeLimit <= 0) {
    String response = formatError(INVALID_TIME_LIMIT, "Invalid time value");
    server.send(404, "application/json", response);
  } else {
    timeLimit = newTimeLimit;
    writeToEEPROM(LIMIT_ADDR, timeLimit);
    server.send(200);
  }
  blinkStatusLed();
}

// Resumes a given stopped device
void handleResume() {
  String device = server.arg("device");
  char *end;
  long i = strtol(device.c_str(), &end, 10);
  if (device == "" || *end != '\0' || i > DEVICES_NUMBER - 1 || i < 0) {
    String response = formatError(INVALID_DEVICE, "Invalid device number");
    server.send(404, "application/json", response);
  } else if (devicesData[i].status != STOPPED) {
    String response = formatError(DEVICE_NOT_STOPPED, "The selected device is not in forced stop state");
    server.send(404, "application/json", response);
  } else {
    digitalWrite(OUTPUTS_PINS[i], LOW);
    devicesData[i].currentTime = 0;
    devicesData[i].status = OFF;
    server.send(200);
  }
  blinkStatusLed();
}

// Returns a not found message to the client, formatted as a JSON string
void handleNotFound() {
  String response = formatError(NOT_FOUND, "URL not found");
  server.send(404, "application/json", response);
  blinkStatusLed();
}

// Sets the WiFi configuration
void handleSetWiFiConfig() {
  String ssid = server.arg("ssid");
  String password = server.arg("password");

  if (ssid == "" || ssid.length() > 32) {
    String response = formatError(INVALID_WIFI_SSID, "Invalid WiFi SSID");
    server.send(400, "application/json", response);
    blinkStatusLed();
    return;
  }

  if (password == "" || password.length() < 8 || password.length() > 64) {
    String response = formatError(INVALID_WIFI_PASSWORD, "Invalid WiFi password");
    server.send(400, "application/json", response);
    blinkStatusLed();
    return;
  }

  server.send(200);
  blinkStatusLed();

  connectToWiFi(ssid, password, STATUS_LED);
}

// Gets the WiFi configuration
void handleGetWiFiConfig() {
  String response = formatWiFiConfig(WiFi.SSID());

  server.send(200, "application/json", response);
  blinkStatusLed();
}

// Gets the current WiFi status
void handleGetWiFiStatus() {
  String response = formatWiFiStatus(WiFi.localIP().isSet() ? WiFi.localIP().toString() : "", WiFi.status());

  server.send(200, "application/json", response);
  blinkStatusLed();
}

// Returns an HTML page to the client, to manage and see the WiFi configuration
void handleAdmin() {
  server.send(200, "text/html", ADMIN_HTML);
  blinkStatusLed();
}

// Set the status LED to blink, updating it's state variables
void blinkStatusLed() {
  digitalWrite(STATUS_LED, HIGH);
  lastLedTimestamp = millis();
  isLedBlinking = true;
}

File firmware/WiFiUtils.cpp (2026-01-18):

#include <ESP8266WiFi.h>
#include "WiFiUtils.h"

const int MAX_AWAIT_TIME = 10;

bool isWiFiConnected() {
  return WiFi.status() == WL_CONNECTED;
}

void awaitWiFiConnection(int ledPin) {
  Serial.println("Connecting to WiFi");
  for (int i = 0; i < MAX_AWAIT_TIME; i++) {
    if (isWiFiConnected()) {
      break;
    }
    digitalWrite(ledPin, LOW);
    delay(500);
    Serial.print(".");
    digitalWrite(ledPin, HIGH);
    delay(500);
  }
  Serial.println();

  if (isWiFiConnected()) {
    Serial.println("WiFi connected");
    Serial.println("IP address: ");
    Serial.println(WiFi.localIP());
  } else {
    Serial.println("WiFi connection failed");
  }
}

void connectToWiFi(String ssid, String password, int ledPin) {
  WiFi.begin(ssid, password);
  awaitWiFiConnection(ledPin);
}

void connectToWiFi(int ledPin) {
  WiFi.begin();
  awaitWiFiConnection(ledPin);
}

void beginWiFi(String ssidAP, String passwordAP, int ledPin) {
  WiFi.mode(WIFI_AP_STA);
  WiFi.softAP(ssidAP, passwordAP);
  WiFi.persistent(true);
  connectToWiFi(ledPin);
}

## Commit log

2023-05-20 Add StatusCard and ButtonWithIcon components
2023-09-10 Add new sensor status indicator design
2023-09-10 Add sensor status indicator
2023-09-17 Add status LED blink behaviour
2023-09-17 Fix bug reading history from memory
    [firmware.ino]
2023-09-17 Add LED indication for network status
2023-09-20 Reorder modal buttons
2024-02-11 Add circuit and PCB design
    [pcb.kicad_pcb, pcb.kicad_sch]
2024-08-05 Add pcb directory to VSCode workspace
2024-08-06 Add new terminal block model and update PCB design
    [Terminal_block_4.SLDPRT, pcb.kicad_pcb, pcb.kicad_sch]
2024-08-08 Add pin socket model and update PCB
    [Pin_socket_2.SLDPRT, pcb.kicad_pcb, pcb.kicad_sch]
2024-12-20 Fix wrong output status logic
    [firmware.ino]
2024-12-20 Align footprints and PCB components placement
    [pcb.kicad_pcb, pcb.kicad_sch]
2024-12-20 Add PCB ground plane border clearance
    [pcb.kicad_pcb]
2024-12-20 Add PCB layout and schematic PDFs
2024-12-22 Add new optocoupler model
    [optocoupler.SLDASM, optocoupler_box.SLDPRT, optocoupler_box.STL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]
2024-12-22 Update optocoupler footprint and PCB with new model
    [pcb.kicad_pcb, pcb.kicad_sch]
2024-12-22 Update schematic and layout PDFs
2024-12-23 Add power micro USB socket model
    [power_usb_socket.SLDPRT, power_usb_socket.STL]
2024-12-25 Migrate firmware project from Arduino VSCode extension to IDE 2
2024-12-25 Add PCB mounting holes
    [pcb.kicad_pcb]
2024-12-25 Add device IP setting modal design
2024-12-26 Add device IP setting modal and remove .env file IP configuration logic
2024-12-26 Update device IP setting option design
2025-03-03 Invert cancel and accept modal buttons position
2025-03-03 Replace icon for text in HistoryModal button
2025-03-03 Revert "Invert cancel and accept modal buttons position"
    This reverts commit d99ad16db06f1a22daf244c8c2e1e73927201f67.
2025-04-05 Add PCB support 3D model
    [pcb_support.SLDPRT, pcb_support.STL]
2025-04-06 Relocate PCB screw holes
    [pcb.kicad_pcb]
2025-08-14 Update PCB date
    [pcb.kicad_pcb]
2025-08-23 Update PCB support model
    [pcb_support.SLDPRT, pcb_support.STL]
2025-08-23 Add power USB socket washer
    [power_usb_washer.SLDPRT, power_usb_washer.STL]
2025-08-24 Add status LED case
    [status_led_case.SLDPRT, status_led_case.STL]
2025-08-30 Relocate all 3D models to a folder
    [Pin_socket_2.SLDPRT, Terminal_block_4.SLDPRT, optocoupler.SLDASM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]
